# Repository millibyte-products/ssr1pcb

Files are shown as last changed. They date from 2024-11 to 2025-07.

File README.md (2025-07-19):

# SSR1PCB
An ESP32 Motor Control board for the TMAx SR1.
Integrates USB Power Delivery at 100W (use appropriate cabling)

:warning: **This device can use dangerous amounts of power**: Device may become very hot in use and may present a fire hazard. Operate at own risk.
Device can draw up to 100W from a compatible power supply. Ensure all cabling and any power devices are rated for 100W (20V at 5A).
Device may present a shock hazard. Device may present a burn hazard.

## Hardware V1.6
hardware v1.6 pcb Hardware Version 1.6
### USB PD
USB power delivery port can sink up to 5A at 20V, meeting the maximum 100W USB PD standard.
When operated at maximum power, a cable rated for 100W should be used and power supply rated for 100W should be used.
Device does not operate as a power source.

It may be possible to use a 65W power delivery device, or any other supporting 20V delivery, however this may result in degraded performance.

### USB Data
A second usb port is used for data and low voltage programming.
When using this port without the PD port, any motors or other high draw loads should be disconnected from the board.
PD operation will energize the 5V power domain, but is disconnected from the 5V rail of the port.
### External power
The power regulators are exposed through user accessable pins.
A 12V, 5V, 3.3V and PD rail (20V) are exposed.
20V total draw should not exceed 5A.

Note: most 2.54mm headers are not rated for more than 1A per pin. Excercise caution when drawing current from the power rails.
:warning: The 12V power supply is limited to 3A internally, but may be limited by the maximum power of the PD interface during operation.
:warning: The 5V power supply is limited to 3A internally, but may be limited by the maximum power of the PD interface during operation. The 3V3 supply depends on the 5V rail, and may be adversely effected by excessive current draw.
:warning: The 3.3V total draw should not exceed 500mA. Using the 3.3V power rail may adversely effect the operation of the ESP32.

Fan voltage may be selected by using the on board switch. Voltage is switchable between 5V and 12V. Do not use a 5V rated fan with a selected voltage of 12V.
## Pinout
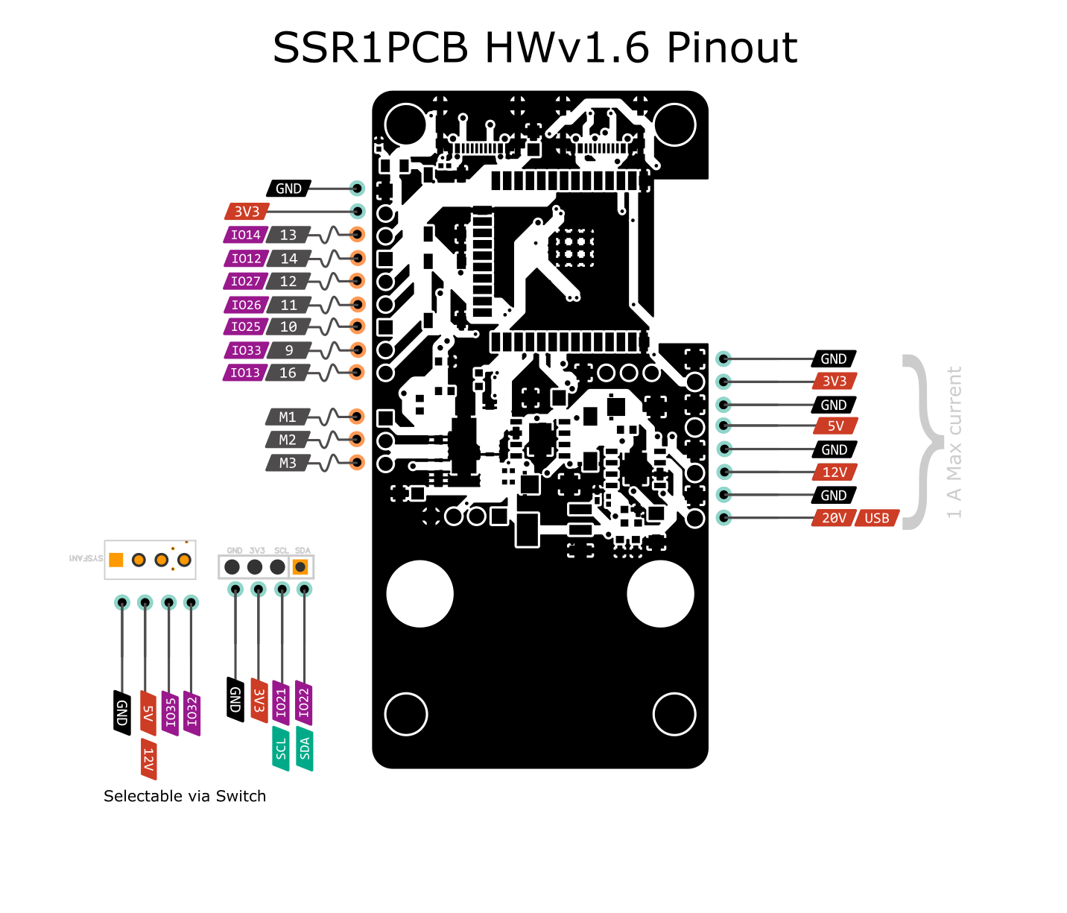
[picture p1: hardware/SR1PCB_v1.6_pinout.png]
hwv1.6 pinouts Pinouts

1) ESP32 uses multiplexed peripherals, hardware assignments are recomended
2) SPI (vspi) Pins required to access encoder
:warning: The labels on the PCB do not correspond to GPIOs

| Pin | Board Label | Arduino GPIO | Function/Description |
| --- | --- | --- | --- |
| 7 | - | GPIO35 | FAN TACH |
| 8 | - | GPIO32 | FAN PWM |
| 9 | IO4 | GPIO33 | User IO 4 |
|  10 | IO3 | GPIO25 | User IO 3 |
|  11 | IO2 | GPIO26 | User IO 2 |
|  12 | IO1 | GPIO27 | User IO 1 |
|  13 | HALL | GPIO14 | User / Hall Effect |
|  14 | IO0 | GPIO12 | User IO 0 |
|  13 | IO5 | GPIO13 | User IO 5 |
|  23 | - | GPIO15 | FOC N_FAULT |
|  24 | - | GPIO2 | FOC IN1 |
|  25 | BOOT | BOOT | BOOT |
|  26 | - | GPIO4 | FOC Enable |
|  27 | - | GPIO16 | FOC IN2 |
|  28 | - | GPIO17 | FOC IN3 |
|  29 | - | GPIO5 | SSI/SPI CS |
|  30 | - | GPIO18 | SSI/SPI CLK |
|  31 | - | GPIO19 | SSI DATA/SPI MISO |
|  33 | SCL | GPIO21 | I2C SCL |
|  34 | - | RXD0 | UART (usb reserved)  |
|  35 | - | TXD0 | UART (usb reserved)  |
|  36 | SDA | GPIO22 | I2C SDA |

## Peripherals
Onboard peripherals include 
* MT6701QT-STD rotary encoder in SSI mode, wired to vpsi interface (GPIO5,18,19)
* DRV8313PWPR FOC controller (GPIO2,4,16,17)
* CP2102-GMR USB-UART transcoder/controller (TX,RX)

## Software
We recommend the use of [TCodeESP32 firmware](https://github.com/jcfain/TCodeESP32).
After flashing the device and configuring the wifi, navigate to the settings page (tcode.local or via the device IP) and select SSR1PCB from the device type dropdown. The device must be restarted before settings will apply.

### Basic firmware
See [firmware](firmware/) folder for basic TCode implementation.
Built with Platformio, see [platformio.org](https://platformio.org/) for documentation.

#### Flashing
Obtain [esptool](https://github.com/espressif/esptool/releases) or if you don't have  a python installation, try [esptool-standalone](https://github.com/mgiachetti/esptool-standalone)
Download a [release binary](https://github.com/millibyte-products/ssr1pcb/releases/latest/download/firmware-blob.zip)
Unzip and open a command-line/terminal in the unzipped folder.
`esptool` must be on your system `PATH`.
Execute `flash.bat` or `flash.sh`, whichever is appropriate for your operating system.

Alternatively, execute the following from that command line:
```
esptool.exe --chip esp32 --baud 460800 --before default_reset --after hard_reset write_flash -z --flash_mode dio --flash_freq 40m --flash_size detect 0x1000 bootloader.bin 0x8000 partitions.bin 0xe000 boot_app0.bin 0x10000 firmware.bin
```

### Troubleshooting/FAQ
:warning:
#### My motor wont spin
Check that the 20V rail is powered (USB PC) with a source that is 100W certified.
Ensure cable used is 100W certified.
#### My motor wont spin/vibrates
Check that you have not screwed too far into the motor and damaged the coils.
Replace motor if so.
#### My motor spins initially, then just vibrates
Check encoder magnet orientation. Incorrect orientation will cause unpredictable motor behavior. N/S poles must be orthogonal to encoder.
A cube magnet is recommended for ease of alignment. Rotate your magnet until a configuration works. Disk magnets may be oriented long-ways (in this case, it is recommended to replace the magnet with a cube magnet)
#### (HWv1.3) My device is stuck in bootloader when connected to PD only
This is a hardware bug. It is fixed in HWv1.4 or later. Do not follow these insructions for HWv1.4+
Pressing the reset (EN) button should reboot the device into normal operation.
Users may remove C8 (on the underside, near the usb ports) at their own risk. Desolder the cap, or cut it, being careful not to damage the pads or traces.

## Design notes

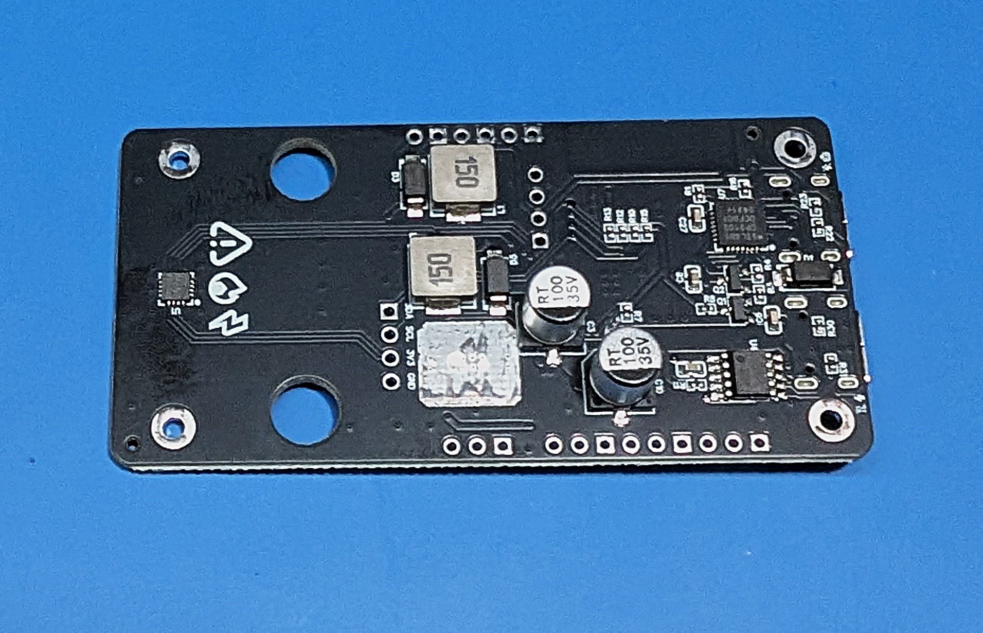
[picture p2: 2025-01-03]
hardware/HW_Back_1.3.jpg

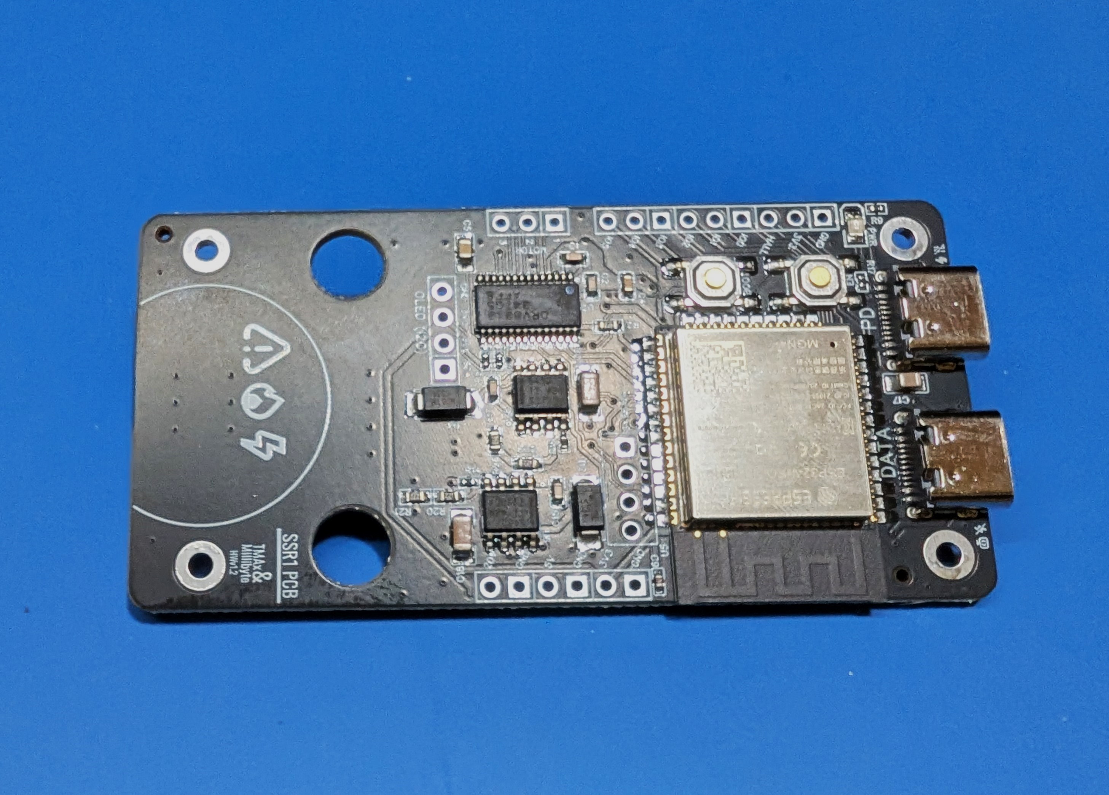
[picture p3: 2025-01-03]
hardware/HW_Front_1.3.jpg

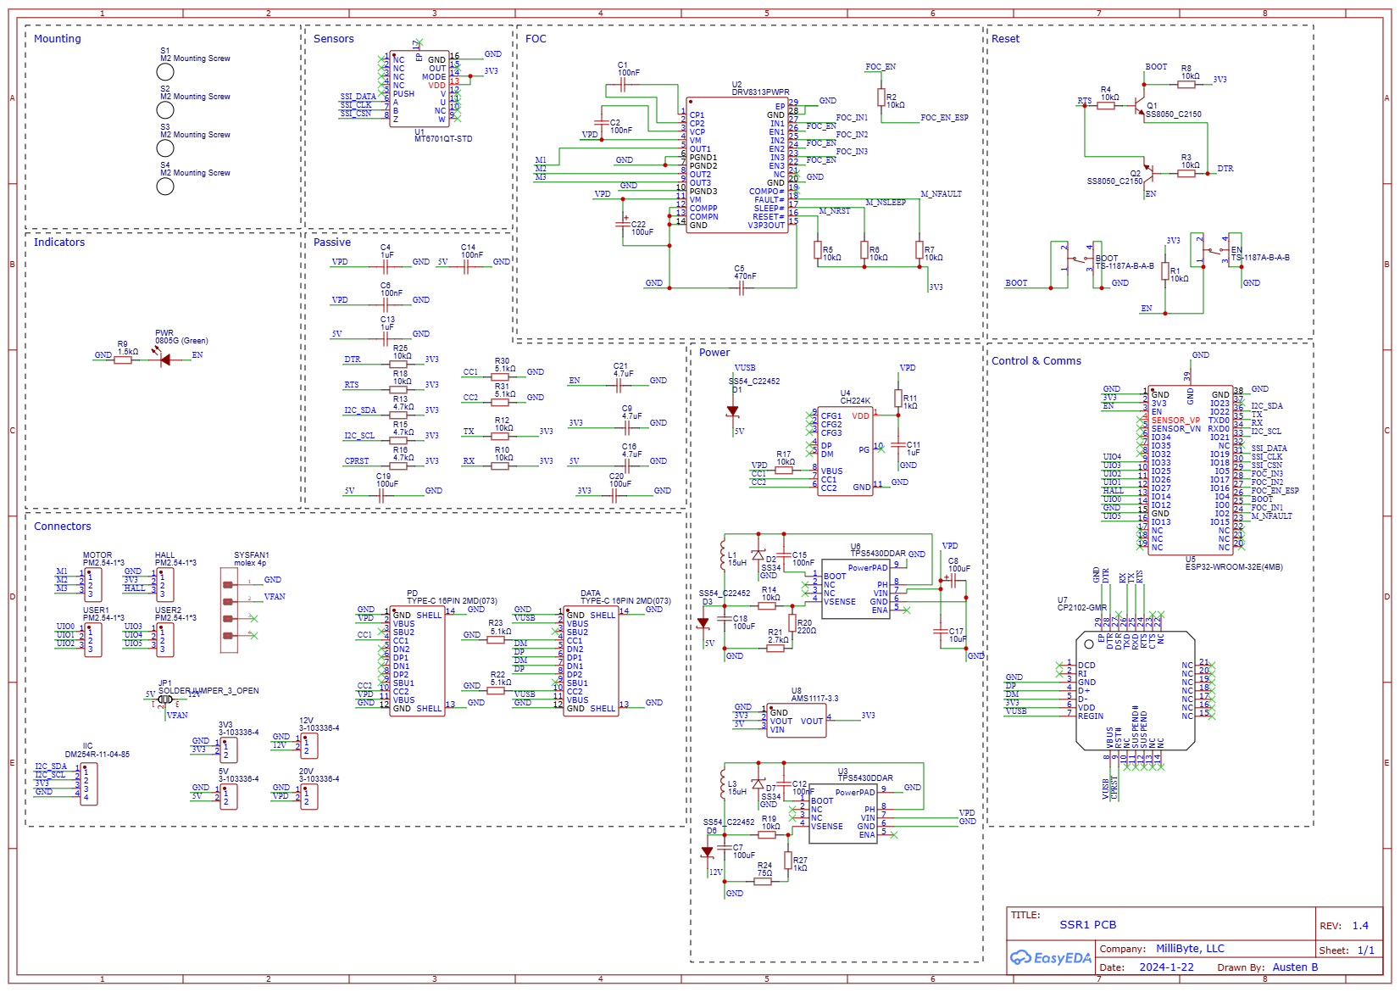
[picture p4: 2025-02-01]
beta/Schematic_SCore-SR1_2025-01-31.png

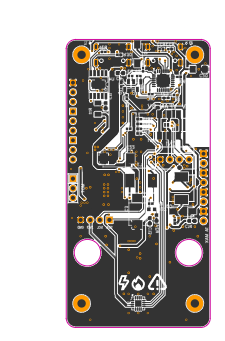
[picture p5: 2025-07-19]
PCB_PCB_SR1PCB_2025-07-19_back.png

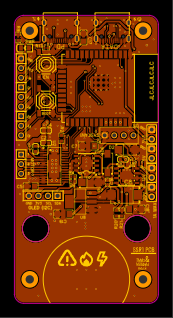
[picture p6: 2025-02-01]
PCB_PCB_SR1PCB_2025-01-31.png

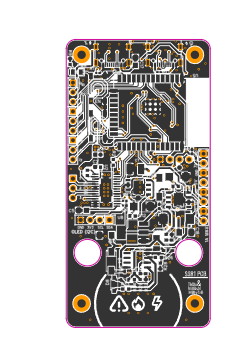
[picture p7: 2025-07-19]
PCB_PCB_SR1PCB_2025-07-19_front.png

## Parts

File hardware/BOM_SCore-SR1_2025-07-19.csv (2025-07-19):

ID | Name | Designator | Footprint | Quantity | Manufacturer Part | Manufacturer | Supplier | Supplier Part | Price
1 | 470533000 | CN1 | CONN-TH_4P-P2.54_0470533000 | 1 | 470533000 | MOLEX | LCSC | C19795120 | 0.323
2 | 1kΩ | R11 | R1206 | 1 | 1206W4F1001T5E | UNI-ROYAL(厚声) | LCSC | C4410 | 0.003
3 | SS54 | D3,D6 | SMA_L4.4-W2.8-LS5.4-R-RD | 2 | SS54 | MDD | LCSC | C22452 | 0.044
4 | PZ2.54-1*3 | MOT | HDR-TH_3P-P2.54-V-M | 1 | PZ2.54-1*3 | ZHOURI(洲日) | LCSC | C5360899 | 0.019
5 | MS-22D17-G2 | SW1 | SW-SMD_DEALON_MS-22D17-G2 | 1 | MS-22D17-G2 | DEALON(德艺隆) | LCSC | C2904912 | 0.093
6 | 15uH | L1,L3 | IND-SMD_L7.3-W6.8 | 2 | MWSA0603S-150MT | Sunlord(顺络) | LCSC | C408452
7 | 100uF | C22,C3,C8 | CAP-SMD_L7.3-W4.3-R-RD | 3 | 20TQC100MYF | PANASONIC(松下) | LCSC | C139578 | 0.796
8 | 10kΩ | R18,R25,R14,R19,R1,R3,R4,R7,R8,R10,R12,R5,R6,R17 | R0402 | 14 | 0402WGF1002TCE | UNI-ROYAL(厚声) | LCSC | C25744 | 0.001
9 | 1uF | C13,C11,C4 | C0603 | 3 | CL10A105KB8NNNC | SAMSUNG(三星) | LCSC | C15849 | 0.005
10 | 100nF | C14,C6,C12,C15,C1,C2 | C0603 | 6 | CC0603KRX7R9BB104 | YAGEO(国巨) | LCSC | C14663 | 0.002
11 | 75Ω | R24 | R0603 | 1 | 0603WAF750JT5E | UNI-ROYAL(厚声) | LCSC | C4275 | 0.001
12 | 1kΩ | R27 | R0603 | 1 | 0603WAF1001T5E | UNI-ROYAL(厚声) | LCSC | C21190 | 0.001
13 | 5.1kΩ | R22,R23,R30,R31 | R0402 | 4 | 0402WGF5101TCE | UNI-ROYAL(厚声) | LCSC | C25905 | 0.001
14 | SS54_C22452 | D1,D4 | SMA_L4.4-W2.8-LS5.4-R-RD | 2 | SS54 | MDD | LCSC | C22452 | 0.044
15 | CH224K | U4 | ESSOP-10_L4.9-W3.9-P1.0-LS6.0-TL-EP | 1 | CH224K | WCH(南京沁恒) | LCSC | C970725 | 0.509
16 | CP2102-GMR | U7 | WQFN-28_L5.0-W5.0-P0.50-BL-EP3.2 | 1 | CP2102-GMR | SKYWORKS/SILICON LABS(芯科) | LCSC | C6568 | 2.091
17 | SS8050_C2150 | Q1,Q2 | SOT-23-3_L2.9-W1.3-P1.90-LS2.4-BR | 2 | SS8050 | CJ(江苏长电/长晶) | LCSC | C2150 | 0.013
18 | MT6701QT-STD | U1 | QFN-16_L3.0-W3.0-P0.50-TL-EP | 1 | MT6701QT-STD | MagnTek(麦歌恩) | LCSC | C2913974 | 1.418
19 | 4.7kΩ | R13,R15,R16 | R0402 | 3 | 0402WGF4701TCE | UNI-ROYAL(厚声) | LCSC | C25900 | 0.001
20 | 4.7uF | C21,C16,C9 | C0402 | 3 | CL05A475MP5NRNC | SAMSUNG(三星) | LCSC | C23733 | 0.005
21 | 100uF | C20,C19,C18 | C1206 | 3 | CL31A107MQHNNNE | SAMSUNG(三星) | LCSC | C15008 | 0.067
22 | TYPE-C 16PIN 2MD(073) | DATA | USB-C-SMD_TYPE-C-6PIN-2MD-073 | 1 | TYPE-C 16PIN 2MD(073) | SHOU HAN(首韩) | LCSC | C2765186 | 0.058
23 | TYPE-C 16PIN 2MD(073) | PD | USB-C-SMD_TYPE-C-6PIN-2MD-073 | 1 | TYPE-C 16PIN | SHOU HAN(首韩) | LCSC | C2765186 | 0.058
24 | BZT52C5V6S_C910052 | D5 | SOD-323_L1.8-W1.3-LS2.5-RD | 1 | BZT52C5V6S | FUXINSEMI(富芯森美) | LCSC | C910052 | 0.013
25 | 1N4148W | D8 | SOD-123F_L2.7-W1.6-LS3.8-RD | 1 | 1N4148W | ST(先科) | LCSC | C81598 | 0.011
26 | SI2301CDS-T1-GE3 | Q3 | SOT-23-3_L3.0-W1.7-P0.95-LS2.9-BR | 1 | SI2301CDS-T1-GE3 | VISHAY(威世) | LCSC | C10487 | 0.057
27 | 47kΩ | R26 | R0603 | 1 | 0603WAF4702T5E | UNI-ROYAL(厚声) | LCSC | C25819 | 0.001
28 | 10kΩ | R28,R32,R2 | R0603 | 3 | 0603WAF1002T5E | UNI-ROYAL(厚声) | LCSC | C25804 | 0.001
29 | 100kΩ | R29 | R0603 | 1 | 0603WAF1003T5E | UNI-ROYAL(厚声) | LCSC | C25803 | 0.001
30 | 1MΩ | R33 | R0603 | 1 | 0603WAF1004T5E | UNI-ROYAL(厚声) | LCSC | C22935 | 0.001
31 | 4.7kΩ | R34 | R0603 | 1 | 0603WAF4701T5E | UNI-ROYAL(厚声) | LCSC | C23162 | 0.001
32 | 0Ω | R35 | R1206 | 1 | 1206W4F0000T5E | UNI-ROYAL(厚声) | LCSC | C17888 | 0.003
33 | LM393DR2G | U10 | SOIC-8_L5.0-W4.0-P1.27-LS6.0-BL | 1 | LM393DR2G | onsemi(安森美) | LCSC | C7955 | 0.091
34 | 100uF | C7 | C1210 | 1 | HGC1210R5107M160NSVK | Chinocera(华瓷) | LCSC | C7432790 | 0.384
35 | 1.5kΩ | R9 | R0603 | 1 | 0603WAF1501T5E | UNI-ROYAL(厚声) | LCSC | C22843 | 0.001
36 | SS34 | D7,D2 | SMA_L4.3-W2.6-LS5.2-RD | 2 | SS34 | MDD(辰达半导体) | LCSC | C8678 | 0.028
37 | TPS5430DDAR | U3,U6 | ESOP-8_L4.9-W3.9-P1.27-LS6.0-TL-EP | 2 | TPS5430DDAR | TI(德州仪器) | LCSC | C9864 | 0.306
38 | AMS1117-3.3 | U8 | SOT-223-3_L6.5-W3.4-P2.30-LS7.0-BR | 1 | AMS1117-3.3 | AMS | LCSC | C6186 | 0.174
39 | 470nF | C5 | C0805 | 1 | CL21B474KBFNNNE | SAMSUNG(三星) | LCSC | C13967 | 0.014
40 | 220Ω | R20 | R0603 | 1 | 0603WAF2200T5E | UNI-ROYAL(厚声) | LCSC | C22962 | 0.001
41 | 2.7kΩ | R21 | R0603 | 1 | 0603WAF2701T5E | UniOhm | LCSC | C13167 | 0.001
42 | ESP32-WROOM-32E(4MB) | U5 | WIFI-SMD_ESP32-WROOM-32E | 1 | ESP32-WROOM-32E-N4 | ESPRESSIF(乐鑫) | LCSC | C701341 | 3.713
43 | 10uF | C17 | C0805 | 1 | CL21A106KAYNNNE | SAMSUNG(三星) | LCSC | C15850 | 0.011
44 | DRV8313PWPR | U2 | HTSSOP-28_L9.8-W4.5-P0.65-LS6.6-BL-EP | 1 | DRV8313PWPR | Texas Instruments | LCSC | C92482 | 1.905
45 | TS-1187A-B-A-B | BOOT,EN | SW-SMD_4P-L5.1-W5.1-P3.70-LS6.5-TL-2 | 2 | TS-1187A-B-A-B | XKB Connectivity(中国星坤) | LCSC | C318884 | 0.019
46 | 0805G (Green) | PWR | LED0805-R-RD | 1 | KT-0805G | KENTO | LCSC | C2297 | 0.011

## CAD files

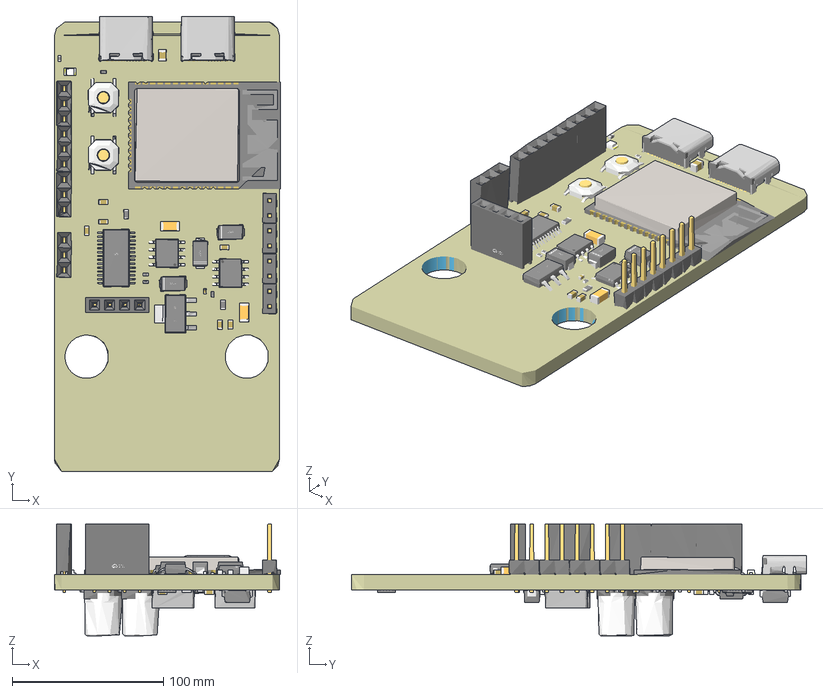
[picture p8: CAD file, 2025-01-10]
HWv1.3/OBJ_PCB_SR1PCB_1.3.3mf
149.5 x 300.8 x 74.0 mm

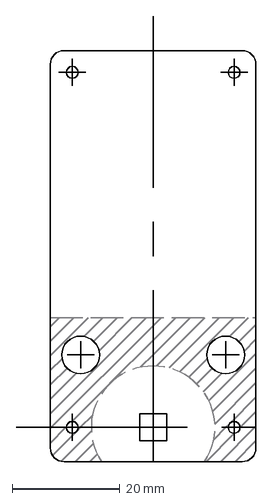
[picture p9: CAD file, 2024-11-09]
SSR1 PCB.dxf
44.5 x 82.6 mm

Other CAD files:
Legacy/HWv1/PCB-SR1001.stl
HWv1.3/OBJ_PCB_SR1PCB_1.3.obj
HWv1.3/OBJ_PCB_SR1PCB_1.3.stl
Legacy/HWv1.3/OBJ_PCB_SR1PCB_1.3.obj
Legacy/HWv1.3/OBJ_PCB_SR1PCB_1.3.stl

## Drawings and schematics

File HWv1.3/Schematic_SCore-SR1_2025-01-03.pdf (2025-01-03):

## Mounting

## Indicators

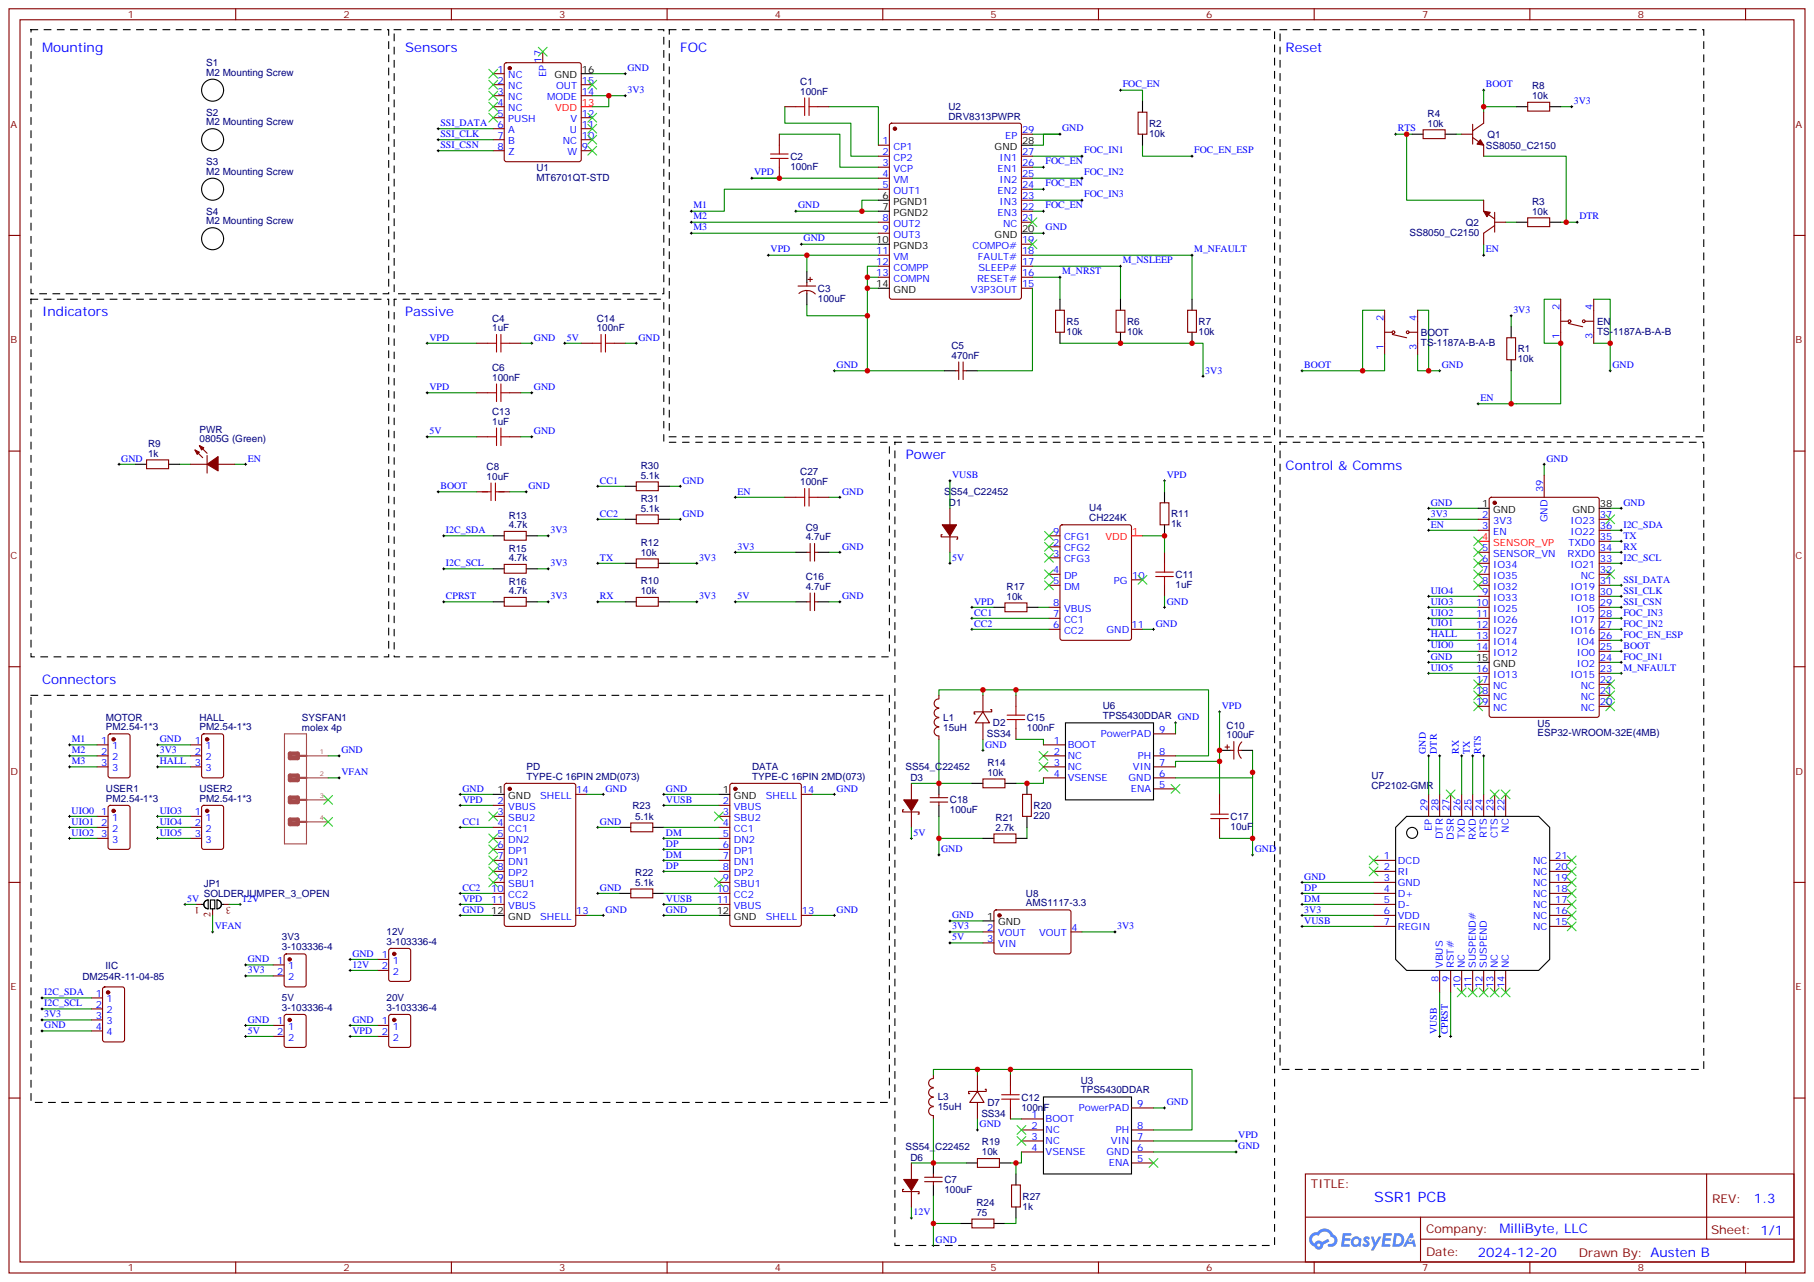
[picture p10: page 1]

12 VDD 13 MODE 14 OUT 15 GND 16

NC 22 CTS 23 RTS 24 RXD 25 TXD 26 DSR 27 DTR 28 EP 29 RXTX

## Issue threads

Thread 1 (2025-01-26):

DTR line pulled low when Power Delivery is connected without connecting Data

millibyte-products, 2025-01-26:
The DTR line appears to be pulling BOOT low when PD is connected without a data line.
This is problematic for WIFI as it leaves the device in the bootloader.

Possible fixes:
1) Add a pullup on DTR line
2) Cut the DTR line (will disable auto boot)
3) Dummy plug in data port (VUSB rail to power CP2102)

millibyte-products, 2025-01-31:
Caused by a unnecessary cap on the boot line.
HW revisions will remove this cap, and it can be removed by users (be careful not to damage the pads) at their own risk.
A pullup will also be added to the DTR and RTS lines to prevent cases where the would be left floating.

nelrock101, 2025-01-31:
I have ordered one of the boards it did not ship yet would the board ordered come with the cap removed? If not what cap would need to be removed?

Closed 2025-01-31.

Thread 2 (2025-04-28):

More of a request than an issue

SoLongSidekick, 2025-04-28:
Having trouble finding the gimbal motor but I do have both a normal 12v DC motor w/ a typical 6-lead encoder (R-B-Gr-Bl-Y-Wh harness color coding) and one without and the SSR1 PCB, what changes to the stock code would be needed and how would it be wired?

millibyte-products, 2025-04-28:
Hello!
You're looking at some serious changes to use a custom encoder and brushed motor.
Unfortunately, you may need some external circuitry to convert the triple half-H bridge to a single bi-directional H-bridge.
I'm not sure a software-only change can manage it. Off the top of my head, I don't have any real advice for this one, sorry.
For the encoder, if it's analog you'll need to enable pulse counting on some of the user GPIO pins and follow the circuit diagram that came with your motor/encoder.

-Millibyte Staff

millibyte-products, 2025-04-28:
Page 20 of the Datasheet suggests that it may be as simple as connecting brushed motor driver terminals to MOT 1 and MOT 2.
However I'm not sure the software supports this operation, since it wouldn't be field-oriented control. You'd want to find an alternative DRV8313 library that allows this configuration.
You'll also want to limit output voltage in software to 12Vs, from a supply voltage of 20V.

Closed 2025-05-25.

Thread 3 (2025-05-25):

Ok now I do have an issue, dead PCB possibly

SoLongSidekick, 2025-05-25:
FInally got a suitable motor and plugged everything in... nothing. No output to the motor nothing initializes on a little 1306 oled I had laying around (yes, pinout confirmed). How can I test to see if my unit is functional?

SoLongSidekick, 2025-06-21:
I don' know it isn't a software bug, that's why I'm starting here. How can I diagnose the issue?

Closed 2025-06-08.

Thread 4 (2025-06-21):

How to diagnose hardware failure vs firmware vs whatever?

SoLongSidekick, 2025-06-21:
I can't reopen my other issue I guess so I made this one.

Upon booting up with the correct gimbal motor mounted inline where it should be I get status LEDs but no motor movement. I've tried swapping the lines and confirming continuity. Is there a way I can export a log?

SoLongSidekick, 2025-07-05:
Nice instructions, prick. Give me my money back for this useless POS.

millibyte-products, 2025-07-05:
Github is not the correct avenue for user-support.
If you wish to start a product return please reach out to store@millibyte.io.
If you are having trouble with an SSR1 build, we recommend the Tempest Max discord as a resource.

Closed 2025-06-21.

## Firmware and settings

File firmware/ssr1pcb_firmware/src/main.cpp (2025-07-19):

// SSR1-P_TCode_ESP32_Beta1
// by TempestMAx 20-11-2024
// Please copy, share, learn, innovate, give attribution.
// Decodes T-code commands and uses them to control servos a single brushless
// motor It can handle:
//   3x linear channels (L0, L1, L2)
//   3x rotation channels (R0, R1, R2)
//   3x vibration channels (V0, V1, V2)
//   3x auxilliary channels (A0, A1, A2)
// This code is designed to drive the SSR1 stroker robot, but is also intended
// to be used as a template to be adapted to run other t-code controlled arduino
// projects Have fun, play safe! History: Alpha1 - First release. 2-2-2023
// Alpha2 - Encoder moved to PIN33, End switch pin removed and start sequence
// changed. 23-2-2023 Alpha3 - SPI feedback by default added. PWM feedback
// switched to the native SFOC function. "Magic numbers" moved to the top of the
// code.
//          Code extensively tided up and comments added/improved. 16-5-2023
// Alpha4 - SSI feedback from MT6701 now default, but AS5048a still supported.
// 28-6-2023 Beta1 - Switch to ESP32-S3-Zero, all pins changed. Only MT6701
// tested so far! 20-11-2024

// ----------------------------
//  User Settings
// ----------------------------
// These are the setup parameters for the SSR1 on an ESP32

// Device IDs, for external reference
#define FIRMWARE_ID \
    "SSR1-P_TCode_ESP32_Beta1.ino"  // Device and firmware version
#define TCODE_VER "TCode v0.3"      // Current version of TCode

// Set to 00000000 for no PCB
#define PCB_VERSION 000103000

#define Encoder_PWM_PIN -1  // PWM feedback pin (if used) - P pad on AS5048a
#define ChipSelect_PIN \
    5  // SPI chip select pin - CSn on AS5048a (By default on ESP32-S3: MISO =
        // D13, MOSI = D11, CLK = D12)
#define Enable_PIN 4       // Motor enable - EN on SFOCMini
#define PWMchannel1_PIN 2  // Motor channel 1 - IN1 on SFOCMini
#define PWMchannel2_PIN 16  // Motor channel 2 - IN2 on SFOCMini
#define PWMchannel3_PIN 17  // Motor channel 3 - IN3 on SFOCMini
// HACK FOR PCB v1.2
#define SSIData_PIN 19
#define SSIClock_PIN 18

// Drive Parameters
#define MotorA_Supply 20
#define MotorA_Voltage 20  // Motor operating voltage (16-20V)
#define MotorA_Current 1   // Maximum operating current (Amps)
// The control code needs to know the angle of the motor relative to the encoder
// - "Zero elec. angle". If a value is not entered it will perform a quick
// operation on startup to estimate this. This will be displayed in the serial
// monitor each time the device starts up. If the device is noticably faster in
// one direction the angle is out of alignment, try increasing or decreasing it
// by small increments (eg +/- 0.1).
#define MotorA_ParametersKnown \
    false // Once you know the zero elec angle for the motor enter it below and
           // set this flag to true.
#define MotorA_ZeroElecAngle \
    2.15  // This number is the zero angle (in radians) for the motor relative
          // to the encoder.
#define MotorA_SensorDirection \
    Direction::CW  // Do not change. If the motor is showing CCW rotate the
                   // motor connector 180 degrees to reverse the motor.
#define SensorA_UseMT6701 \
    true  // Use the MT6701 encoder via SSI rather than the default AS5048a
          // encoder via SPI.
#define SensorA_UsePWM \
    false  // SPI feedback on the AS5048a is default because it's a lot smoother
           // and quieter! Change this to true if you want to use PWM feedback.

// Control constants
// (a.k.a. magic numbers for Eve)
#define RAIL_LENGTH 125          // Physical maximum travel of the receiver (mm)
#define STROKE_LENGTH 120        // Operating stroke length (mm)
#define PULLEY_CIRCUMFERENCE 60  // Drive pulley circumference (mm)
#define P_CONST 0.002            // Motor PID proportional constant
#define LOW_PASS \
    0.8  // Low pass filter factor for static noise reduction ( number < 1, 0 =
         // none)
// Derived constants
#define ANG_TO_POS                   \
    (10000 * PULLEY_CIRCUMFERENCE) / \
        (2 * 3.14159 * STROKE_LENGTH)  // Number to convert a motor angle to a
                                       // 0-10000 axis position
#define START_OFFSET                              \
    2 * 3.14159 * (RAIL_LENGTH - STROKE_LENGTH) / \
        (2 *                                      \
         PULLEY_CIRCUMFERENCE)  // Offset angle from endstop on startup (rad)

// Other functions
#define MIN_SMOOTH_INTERVAL \
    3  // Minimum auto-smooth ramp interval for live commands (ms)
#define MAX_SMOOTH_INTERVAL \
    100  // Maximum auto-smooth ramp interval for live commands (ms)

// T-Code Channels
#define CHANNELS 3  // Number of channels of each type (LRVA)

// Libraries used
#include <Wire.h>
#include <EEPROM.h>     // Permanent memory
#include <BLDCMotor.h>  // Motor controller code
#include <drivers/BLDCDriver3PWM.h>

#include <SimpleFOCDrivers.h>
#include <encoders/MT6701/MagneticSensorMT6701SSI.h>

// -----------------------------
// Class to handle each axis
// -----------------------------
class Axis {
   public:
    // Setup function
    Axis() {
        // Set default dynamic parameters
        rampStartTime = 0;
        rampStart = 5000;
        rampStopTime = rampStart;
        rampStop = rampStart;

        // Set Empty Name
        Name = "";
        lastT = 0;

        // Live command auto-smooth
        minInterval = MAX_SMOOTH_INTERVAL;
    }

    // Function to set the axis dynamic parameters
    void Set(int x, char ext, long y) {
        unsigned long t = millis();  // This is the time now
        x = constrain(x, 0, 9999);
        y = constrain(y, 0, 9999999);
        // Set ramp parameters, based on inputs
        // Live command
        if (y == 0 || (ext != 'S' && ext != 'I')) {
            // update auto-smooth regulator
            int lastInterval = t - rampStartTime;
            if (lastInterval > minInterval &&
                minInterval < MAX_SMOOTH_INTERVAL) {
                minInterval += 1;
            } else if (lastInterval < minInterval &&
                       minInterval > MIN_SMOOTH_INTERVAL) {
                minInterval -= 1;
            }
            // Set ramp parameters
            rampStart = GetPosition();
            rampStopTime = t + minInterval;
        }
        // Speed command
        else if (ext == 'S') {
            rampStart = GetPosition();  // Start from current position
            int d = x - rampStart;      // Distance to move
            if (d < 0) {
                d = -d;
            }
            long dt = d;  // Time interval (time = dist/speed)
            dt *= 100;
            dt /= y;
            rampStopTime = t + dt;  // Time to arrive at new position
            // if (rampStopTime < t + minInterval) { rampStopTime = t +
            // minInterval; }
        }
        // Interval command
        else if (ext == 'I') {
            rampStart = GetPosition();  // Start from current position
            rampStopTime = t + y;       // Time to arrive at new position
            // if (rampStopTime < t + minInterval) { rampStopTime = t +
            // minInterval; }
        }
        rampStartTime = t;
        rampStop = x;
        lastT = t;
    }

    // Function to return the current position of this axis
    int GetPosition() {
        int x;  // This is the current axis position, 0-9999
        unsigned long t = millis();
        if (t > rampStopTime) {
            x = rampStop;
        } else if (t > rampStartTime) {
            x = map(t, rampStartTime, rampStopTime, rampStart, rampStop);
        } else {
            x = rampStart;
        }
        x = constrain(x, 0, 9999);
        return x;
    }

    // Function to stop axis movement at current position
    void Stop() {
        unsigned long t = millis();  // This is the time now
        rampStart = GetPosition();
        rampStartTime = t;
        rampStop = rampStart;
        rampStopTime = t;
    }

    // Public variables
    String Name;          // Function name of this axis
    unsigned long lastT;  //

   private:
    // Movement positions
    int rampStart;
    unsigned long rampStartTime;
    int rampStop;
    unsigned long rampStopTime;

    // Live command auto-smooth regulator
    int minInterval;
};

// -----------------------------
// Class to manage Toy Comms
// -----------------------------
class TCode {
   public:
    // Setup function
    TCode(String firmware, String tcode) {
        firmwareID = firmware;
        tcodeID = tcode;
        halted = false;

        // Vibe channels start at 0
        for (int i = 0; i < CHANNELS; i++) {
            Vibration[i].Set(0, ' ', 0);
        }
    }

    // Function to name and activate axis
    void RegisterAxis(String ID, String axisName) {
        char type = ID.charAt(0);
        int channel = ID.charAt(1) - '0';
        if ((0 <= channel && channel < CHANNELS)) {
            switch (type) {
                // Axis commands
                case 'L':
                    Linear[channel].Name = axisName;
                    break;
                case 'R':
                    Rotation[channel].Name = axisName;
                    break;
                case 'V':
                    Vibration[channel].Name = axisName;
                    break;
                case 'A':
                    Auxiliary[channel].Name = axisName;
                    break;
            }
        }
    }

    // Function to read off individual bytes as input
    void ByteInput(byte inByte) {
        bufferString += (char)inByte;  // Add new character to string

        if (inByte == '\n' || inByte == '\r') {             // Execute string on newline
            bufferString.trim();          // Remove spaces, etc, from buffer
            executeString(bufferString);  // Execute string
            bufferString = "";            // Clear input string
        }
    }

    // Function to read off whole strings as input
    void StringInput(String inString) {
        bufferString = inString;  // Replace existing buffer with input string
        bufferString.trim();      // Remove spaces, etc, from buffer
        executeString(bufferString);  // Execute string
        bufferString = "";            // Clear input string
    }

    // Function to set an axis
    void AxisInput(String ID, int magnitude, char extension,
                   long extMagnitude) {
        char type = ID.charAt(0);
        int channel = ID.charAt(1) - '0';
        if ((0 <= channel && channel < CHANNELS)) {
            switch (type) {
                // Axis commands
                case 'L':
                    Linear[channel].Set(magnitude, extension, extMagnitude);
                    break;
                case 'R':
                    Rotation[channel].Set(magnitude, extension, extMagnitude);
                    break;
                case 'V':
                    Vibration[channel].Set(magnitude, extension, extMagnitude);
                    break;
                case 'A':
                    Auxiliary[channel].Set(magnitude, extension, extMagnitude);
                    break;
            }
        }
    }

    // Function to read the current position of an axis
    int AxisRead(String ID) {
        int x = 5000;  // This is the return variable
        char type = ID.charAt(0);
        int channel = ID.charAt(1) - '0';
        if ((0 <= channel && channel < CHANNELS)) {
            switch (type) {
                // Axis commands
                case 'L':
                    x = Linear[channel].GetPosition();
                    break;
                case 'R':
                    x = Rotation[channel].GetPosition();
                    break;
                case 'V':
                    x = Vibration[channel].GetPosition();
                    break;
                case 'A':
                    x = Auxiliary[channel].GetPosition();
                    break;
            }
        }
        return x;
    }

    // Function to query when an axis was last commanded
    unsigned long AxisLast(String ID) {
        unsigned long t = 0;  // Return time
        char type = ID.charAt(0);
        int channel = ID.charAt(1) - '0';
        if ((0 <= channel && channel < CHANNELS)) {
            switch (type) {
                // Axis commands
                case 'L':
                    t = Linear[channel].lastT;
                    break;
                case 'R':
                    t = Rotation[channel].lastT;
                    break;
                case 'V':
                    t = Vibration[channel].lastT;
                    break;
                case 'A':
                    t = Auxiliary[channel].lastT;
                    break;
            }
        }
        return t;
    }

    bool isHalted()
    {
        return halted;
    }

   private:
    // Strings
    String firmwareID;
    String tcodeID;
    String bufferString;  // String to hold incomming commands
    bool halted; // Flag to signal motor control to disable

    // Declare axes
    Axis Linear[CHANNELS];
    Axis Rotation[CHANNELS];
    Axis Vibration[CHANNELS];
    Axis Auxiliary[CHANNELS];

    // Function to divide up and execute input string
    void executeString(String bufferString) {
        int index = bufferString.indexOf(' ');  // Look for spaces in string
        while (index > 0) {
            readCmd(
                bufferString.substring(0, index));  // Read off first command
            bufferString = bufferString.substring(
                index + 1);  // Remove first command from string
            bufferString.trim();
            index = bufferString.indexOf(' ');  // Look for next space
        }
        readCmd(bufferString);  // Read off last command
    }

    // Function to process the individual commands
    void readCmd(String command) {
        command.toUpperCase();

        // Switch between command types
        switch (command.charAt(0)) {
            // Axis commands
            case 'L':
            case 'R':
            case 'V':
            case 'A':
                axisCmd(command);
                break;

            // Device commands
            case 'D':
                deviceCmd(command);
                break;

            // Setup commands
            case '$':
                setupCmd(command);
                break;
        }
    }

    // Function to read and interpret axis commands
    void axisCmd(String command) {
        char type = command.charAt(0);  // Type of command - LRVA
        boolean valid = true;  // Command validity flag, valid by default

        // Check for channel number
        int channel = command.charAt(1) - '0';
        if (channel < 0 || channel >= CHANNELS) {
            valid = false;
        }
        channel = constrain(channel, 0, CHANNELS);

        // Check for an extension
        char extension = ' ';
        int index = command.indexOf('S', 2);
        if (index > 0) {
            extension = 'S';
        } else {
            index = command.indexOf('I', 2);
            if (index > 0) {
                extension = 'I';
            }
        }
        if (index < 0) {
            index = command.length();
        }

        // Get command magnitude
        String magString = command.substring(2, index);
        magString = magString.substring(0, 4);
        while (magString.length() < 4) {
            magString += '0';
        }
        int magnitude = magString.toInt();
        if (magnitude == 0 && magString.charAt(0) != '0') {
            valid = false;
        }  // Invalidate if zero returned, but not a number

        // Get extension magnitude
        long extMagnitude = 0;
        if (extension != ' ') {
            magString = command.substring(index + 1);
            magString = magString.substring(0, 8);
            extMagnitude = magString.toInt();
        }
        if (extMagnitude == 0) {
            extension = ' ';
        }

        // Switch between command types
        if (valid) {
            switch (type) {
                // Axis commands
                case 'L':
                    Linear[channel].Set(magnitude, extension, extMagnitude);
                    break;
                case 'R':
                    Rotation[channel].Set(magnitude, extension, extMagnitude);
                    break;
                case 'V':
                    Vibration[channel].Set(magnitude, extension, extMagnitude);
                    break;
                case 'A':
                    Auxiliary[channel].Set(magnitude, extension, extMagnitude);
                    break;
            }
        }
    }

    // Function to identify and execute device commands
    void deviceCmd(String command) {
        int i;
        // Remove "D"
        command = command.substring(1);

        // Look for device stop command
        if (command.substring(0, 4) == "STOP") {
            for (i = 0; i < 10; i++) {
                Linear[i].Stop();
            }
            for (i = 0; i < 10; i++) {
                Rotation[i].Stop();
            }
            for (i = 0; i < 10; i++) {
                Vibration[i].Set(0, ' ', 0);
            }
            for (i = 0; i < 10; i++) {
                Auxiliary[i].Stop();
            }
            halted = true;
        } else {
            // Look for numbered device commands
            int commandNumber = command.toInt();
            if (commandNumber == 0 && command.charAt(0) != '0') {
                command = -1;
            }
            switch (commandNumber) {
                case 0:
                    Serial.println(firmwareID);
                    break;

                case 1:
                    Serial.println(tcodeID);
                    break;

                case 2:
                    halted = false;
                    for (i = 0; i < 10; i++) {
                        axisRow("L" + String(i), 8 * i, Linear[i].Name);
                    }
                    for (i = 0; i < 10; i++) {
                        axisRow("R" + String(i), 8 * i + 80, Rotation[i].Name);
                    }
                    for (i = 0; i < 10; i++) {
                        axisRow("V" + String(i), 8 * i + 160,
                                Vibration[i].Name);
                    }
                    for (i = 0; i < 10; i++) {
                        axisRow("A" + String(i), 8 * i + 240,
                                Auxiliary[i].Name);
                    }
                    break;
            }
        }
    }

    // Function to modify axis preference values
    void setupCmd(String command) {
        int minVal, maxVal;
        String minValString, maxValString;
        boolean valid;
        // Axis type
        char type = command.charAt(1);
        switch (type) {
            case 'L':
            case 'R':
            case 'V':
            case 'A':
                valid = true;
                break;
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
void loop() {
    // Read serial and send to tcode class
    while (Serial.available() > 0) {
        // Send the serial bytes to the t-code object
        tcode.ByteInput(Serial.read());
    }

    // Run motor FOC loop
    motorA.loopFOC();

    // Collect inputs
    // These functions query the t-code object for the position/level at a
    // specified time Number recieved will be an integer, 0-9999
    xLin = tcode.AxisRead("L0");

    // Update sensor position
    float angle;
    sensorA.update();
    angle = sensorA.getAngle();
    // Determine the linear position of the receiver in (0-10000)
    xPosition = (angle - zeroAngle) * ANG_TO_POS;

    // Control by motor voltage
    float motorVoltageNew;
    // If the device is in startup mode roll downwards for two seconds and press
    // against bottom stop. Distance of travel is 12,000 (>10,000) just to make
    // sure that the receiver reaches the bottom.
    if (mode == 0) {
        xLin = map(millis() - startTime, 0, 2000, 0, -12000);
        if (millis() > (startTime + 2000)) {
            mode = 1;
            zeroAngle = angle + START_OFFSET;
        }
        motorVoltageNew = P_CONST * (xLin - xPosition);
        if (motorVoltageNew < -0.5) {
            motorVoltageNew = -0.5;
        }
        // Otherwise set motor voltage based on position error
    } else {
        motorVoltageNew = P_CONST * (xLin - xPosition);
    }
    // Low pass filter to reduce motor noise
    motorVoltage = LOW_PASS * motorVoltage + (1 - LOW_PASS) * motorVoltageNew;
    
    if (tcode.isHalted())
    {
        motorA.disable();
    }
    else
    {
        motorA.move(motorVoltage);
    }
}

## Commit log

2024-11-09 Hardware V1
    [BOM_SCore-SR1_2024-11-09.csv, PickAndPlace_PCB_SCore-SR1_2024-11-09.csv, SCore-SR1_2024-11-09.schdoc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]
2024-11-10 3d models
    [PCB-SR1001.stl]
2025-01-03 HW rev1.2
    [BOM_SCore-SR1_2024-11-09.csv, BOM_SCore-SR1_2024-11-10.csv, PCB-SR1001.stl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]
2025-01-10 3D Objects, readme updates
    [OBJ_PCB_SR1PCB_1.3.3mf, OBJ_PCB_SR1PCB_1.3.stl]
2025-01-31 Firmware voltage and stability updates
    [main.cpp]
2025-02-01 HWv1.4 Design
    [BOM_SCore-SR1_2024-11-09.csv, BOM_SCore-SR1_2024-11-10.csv, BOM_SCore-SR1_2025-01-03.csv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]
2025-02-24 V1.3 cleanup
    [SR1PCB_2025-01-31.schdoc]
2025-04-21 Clean up old files and docs
    [BOM_SCore-SR1_2025-01-03.csv, OBJ_PCB_SR1PCB_1.3.3mf, OBJ_PCB_SR1PCB_1.3.obj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]
2025-07-19 Hardware v1.6 Update
    [BOM_SCore-SR1_2025-07-19.csv, PickAndPlace_PCB_SR1PCB_2025-07-19.csv]
